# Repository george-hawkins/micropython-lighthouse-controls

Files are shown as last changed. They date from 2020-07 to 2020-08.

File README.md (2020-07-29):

MicroPython lighthouse controls
===============================

This project was created with [MicroPython](https://micropython.org/) running on an [ESP32](https://docs.espressif.com/projects/esp-idf/en/latest/esp32/hw-reference/esp32/get-started-devkitc.html) development board. The electronics drive the central mechanism for a toy lighthouse. The main point of this project, however, was to try and make something as close to a consumer product in terms of setup and ease of use.

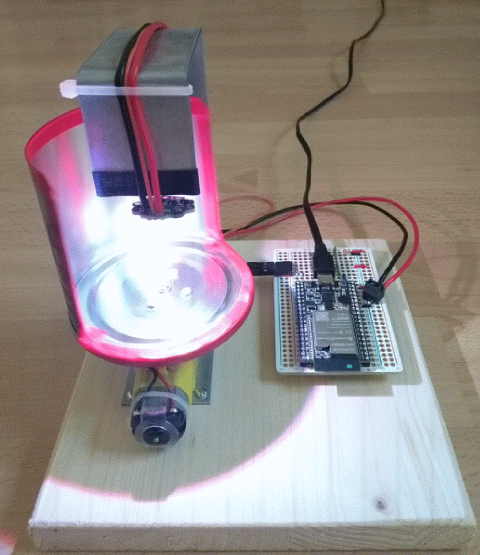
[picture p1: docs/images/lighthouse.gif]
lighthouse animated GIF


There are two main parts to making this device easy to use. The **first** part is connecting it to your network. The following is **not** a screenshot of the standard Android network selection interface. It's a web interface served out by the ESP32 to make it as easy to connect the device to a WiFi network as it is to do the same with your phone.

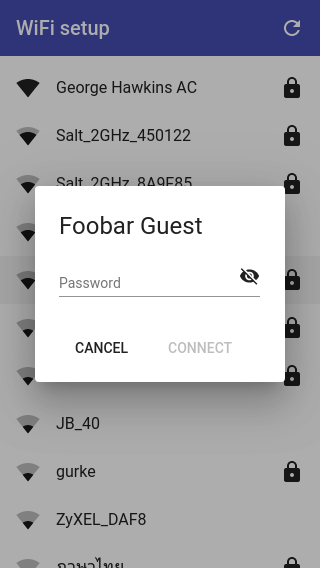
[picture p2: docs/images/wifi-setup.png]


As you may know, MicroPython on the ESP32 supports both an access point (AP) mode (where it behave as an AP that you can connect to) and a station (STA) mode (where it connects to an existing network). If this device cannot connect to an existing network, it creates an open AP that you can connect to and serves out the web interface shown above. Normally, when you create an access point like this, the client that connects to it still has to find the IP address of the device and then connect to that to access such an interface. The clever thing with this project is that it uses your system's captive-portal detection to connect you directly to the web interface when you connect to the network. Captive-portal detection is the same thing that pushes you to the login interface when you connect to public WiFi in places like coffee shops and airports. In this case, instead of a login page, you're presented with a web interface that shows you the networks that the device can see and lets you select the one to which you want to connect it.

The **second** part of making things easy to use is to provide a nice interface for controlling the device once it's connected to the desired network.

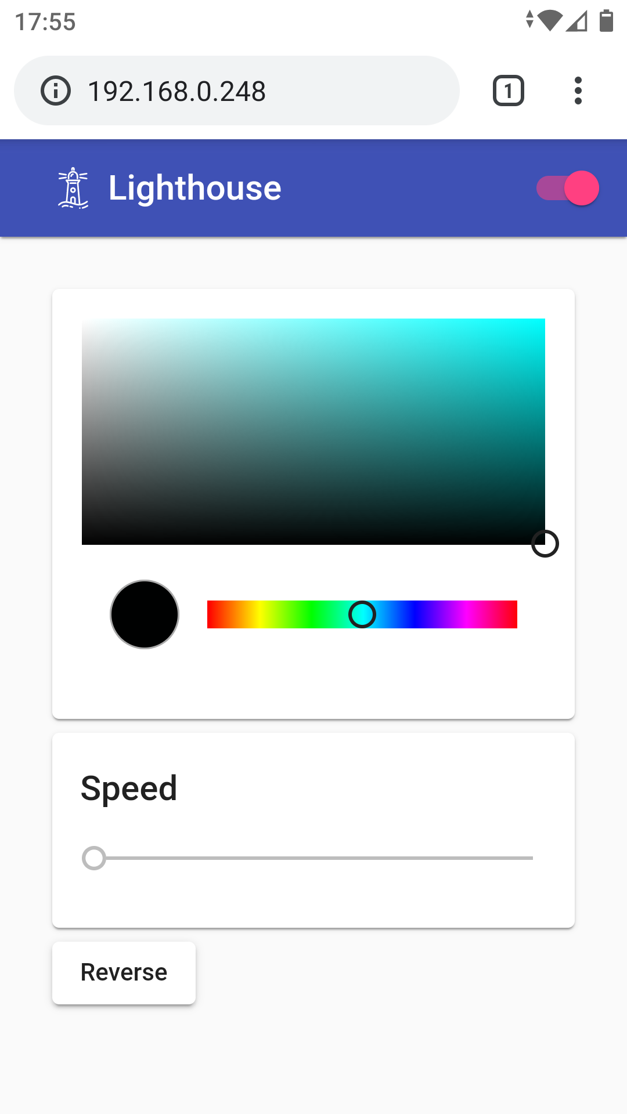
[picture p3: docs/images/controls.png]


Here, things are much easier than with the WiFi setup interface. The HTML etc. for the WiFi setup interface has to be stored locally on the device as, at this point, it has no access to the internet. However, once set up, the web interface for working with the device can be stored remotely (e.g. on GitHub). This saves storage and is also much quicker to load (GitHub being much quicker at serving web pages than an ESP32). A tiny main page for the interface above is retrieved by the device from GitHub and then served out to any requesting client. Then all other requests, related to loading the page, go directly to GitHub. The device serves out the main page (rather than simply doing a redirect) so that all subsequent Javascript etc. sees the device, rather than GitHub, as the origin. This is also important for all the rules related to insecure content loading secure content and vice-versa. It's fine for the device to serve out the main page via HTTP and then include content from GitHub via HTTPS. The opposite is not true, i.e. secure content cannot go on to include insecure content. This is important as the web interface, once served out and running in the client web browser, communicates with the device via a websocket. The websocket connection is insecure, i.e. uses `ws://` rather than `wss://`, and for this to be allowed by the client browser the containing page also has to have been served insecurely.

In the interface above, you can control:

* The brightness and color of the lighthouse light (it uses an RGB LED).
* The speed at which the motor turns.
* The direction the motor turns.

You can also turn off the device (the red slide-toggle), this puts the device into deep sleep.

Code
----

Interestingly, the bulk of the code involved is the WiFi setup code. This code has its own repo - [micropython-wifi-setup](https://github.com/george-hawkins/micropython-wifi-setup/) - where it's described in excessive detail.

The [Angular](https://angular.io/) and [Angular Material](https://material.angular.io/guide/getting-started) resources for the device's user interface (the controls seen above) also have their own repo - [material-lighthouse-controls](https://github.com/george-hawkins/material-lighthouse-controls).

This repo contains the MicroPython code that pulls everything together, it invokes the WiFi setup code and, once set up, it serves out the device's user interface and communicates with it via a websocket. It takes the commands received via the websocket and translates them into hardware actions.

Note: if you look at the code, you'll see that multiple people can open the device's web interface at the same time, each with their own websocket connection to the device. One person can reverse the motor direction while another changes the LED color.

The code here consists of:

* [`main.py`](main.py) - sets up the WiFi connection, controls the RGB LED and motor and handles serving out the web interface and accepting websocket connections.
* [`connect.py`](connect.py) - wraps up calling the WiFi setup logic provided by micropython-wifi-setup.
* [`message_extractor.py`](message_extractor.py) - provides a super-simple message layer on top of the raw websocket connection.

The messages, that I send via the websocket, consist of just a string delimited by the ASCII control characters STX and ETX (start and end of text, respectively). The sending logic in the Angular code contains throttling logic to ensure that it doesn't send messages faster than the device can process them (this would, otherwise, happen in particular when dragging your finger around in the color panel). However, the receiving logic also has logic to deal with this situation - it always tries to read as much data as is currently available and returns just the last message read for further processing, i.e. it will discard earlier messages if multiple messages come in at once. This is an acceptable strategy here as the discarded messages would e.g. be earlier speed values when dragging the speed slider - just processing the latest value is acceptable and is in fact desirable.

Breadboard and perma-proto layout
---------------------------------

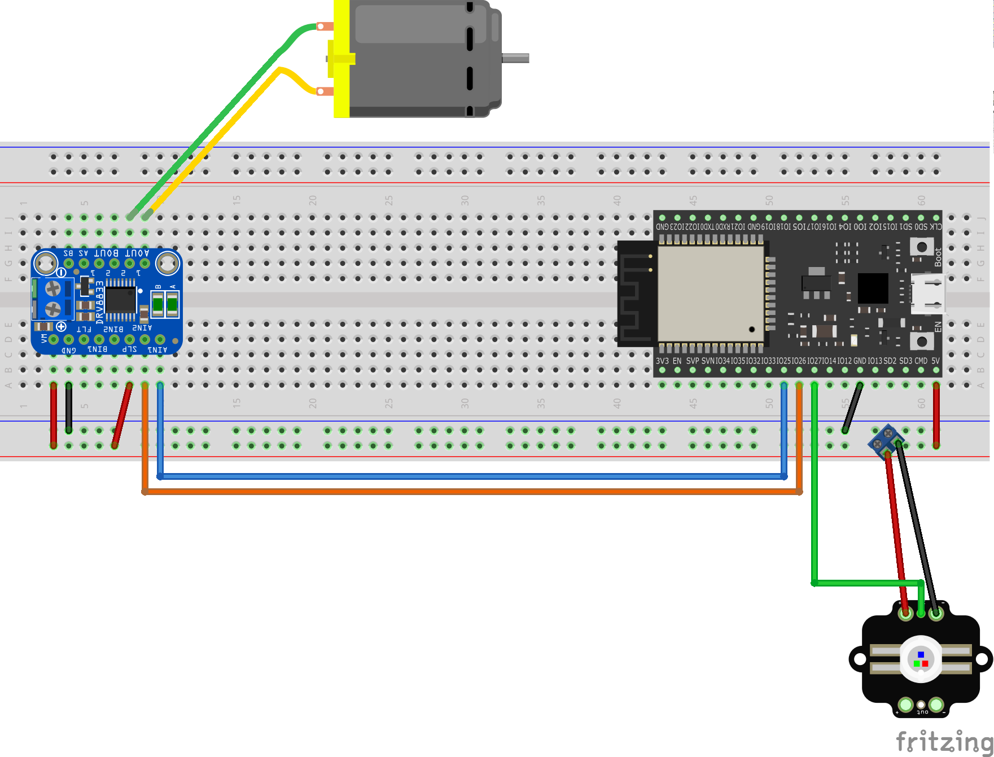
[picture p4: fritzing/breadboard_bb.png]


Fritzing file: [`fritzing/breadboard.fzz`](fritzing/breadboard.fzz)

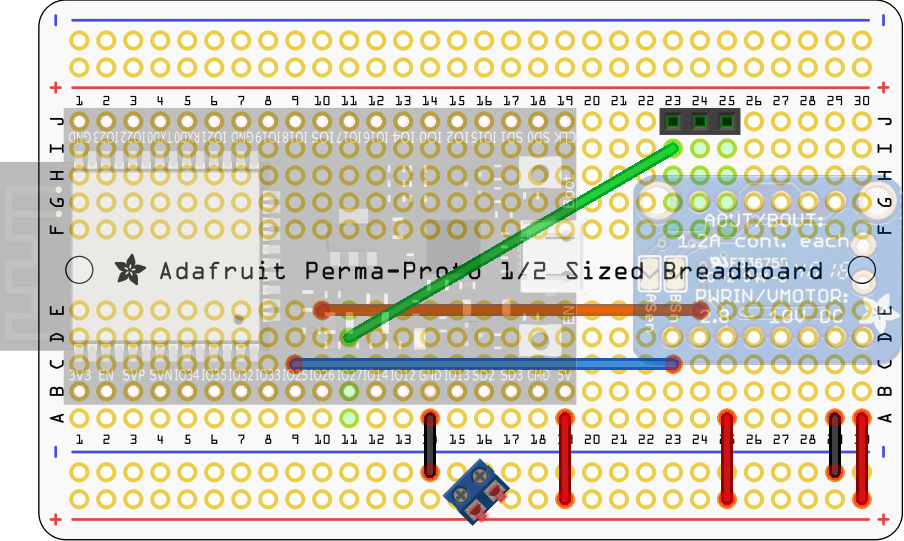
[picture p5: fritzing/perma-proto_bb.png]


Fritzing file: [`fritzing/perma-proto_bb.png`](fritzing/perma-proto_bb.png)

For the perma-proto layout, the DevKitC board was mounted on the top-side of the perma-proto board and the DRV8833 breakout on the underside. They're both shown in very transparent form here, so you can see where they go without obscuring the wiring.

I went for this layout as I wanted the PCB antenna of the DevKitC board to face outward over the edge of the perm-proto board and didn't want the DRV8833 breakout blocking access to the micro-USB connector of the DevKitC board.

All the wiring was done on the top of the perma-proto board except the green wire. Right-angle header was used for the header seen top-right and is where the wires to the motor and the control wire for the RGB LED are connected. The terminal block, seen bottom-center, is for the power wires for the RGB LED.

Note: I included a [0.1uF ceramic capacitor](https://www.adafruit.com/product/753) across the GND and VM pins of the DRV8833 breakout board. This isn't shown in the Fritzing diagrams above, but you can see it clearly in the picture of the top of the perma-proto layout found [here](docs/steps.md). This capacitor was included as a lucky talisman against any noise from the motor - but if the noise was a real problem then the proper way to deal with this would be capacitors soldered across the motor terminals and to its case as shown [here](https://learn.adafruit.com/adafruit-motor-shield-v2-for-arduino/faq) (for more details expand the answer to the question "When the motors start running nothing else works?"). Pololu also have a [page on this](https://www.pololu.com/docs/0J15/9).

I wanted to mount the perma-proto board on the wooden base using spacers with snap-in connectors (rather than the usual screws) but noticed too late that I'd blocked the perma-protos second mounting hole with the DRV8833 breakout board. Snap-in connectors would have allowed the mounting hole under the DevKitC to be used without needing to be able to get at the top-side of the mounting hole (as you would if using screws). It would have been just about possible to position the DRV8833 breakout board such that it didn't block the mounting hole but it would have made everything a very tight fit.

Parts
-----

More parts than you might expect were used in building this setup. The parts and prices are covered in [`docs/parts.md`](docs/parts.md).

Assembly
--------

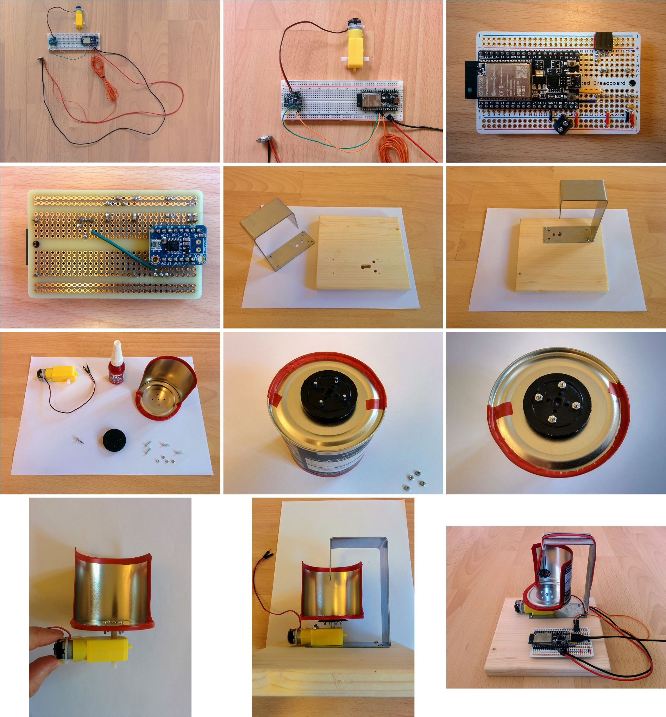
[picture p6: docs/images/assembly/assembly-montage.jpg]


For a step-by-step walkthru of the assembly see [`docs/steps.md`](docs/steps.md).

Installing the code
-------------------

Clone this repo and the micropython-wifi-setup repo and link to its `lib` directory:

    $ git clone git@github.com:george-hawkins/micropython-wifi-setup.git
    $ git clone git@github.com:george-hawkins/micropython-lighthouse-controls.git
    $ cd micropython-lighthouse-controls
    $ ln -s ../micropython-wifi-setup/lib .

Then create a Python venv and install [`rshell`](https://github.com/dhylands/rshell):

    $ python3 -m venv env
    $ source env/bin/activate
    $ pip install --upgrade pip
    $ pip install rshell

Then install everything on your board, start the REPL and then press the _EN_ or _reset_ button on your board:

    $ rshell --buffer-size 512 --quiet -p $PORT
    > mkdir /pyboard/lib
    > cp -r lib/* /pyboard/lib
    > cp main.py connect.py message_extractor.py /pyboard
    > repl
    ...
    I (1567) cpu_start: Pro cpu start user code
    ...
    INFO:captive_portal:captive portal web server and DNS started on 192.168.4.1

Replace `$PORT` with the serial device of your board (typically `/dev/ttyUSB0` on Linux and `/dev/cu.SLAB_USBtoUART` on Mac).

Then connect your device to your network as described in step 2 and onward [here](https://github.com/george-hawkins/micropython-wifi-setup/blob/master/docs/steps.md). At the end, instead of the cute little ghost placeholder shown there, you should see the lighthouse web interface.

Room for improvement
--------------------

At the moment the web interface does not detect if the device has been turned off (interestingly, it fairly quickly notices the issue when the device is started again, at which point it closes and reestablishes the connection). This is covered in more detail in the notes (see below) and could be addressed by sending heartbeats in both directions (from browser to device and vice-versa).

It would be nice to use mDNS, rather than raw IP addresses, where supported (i.e. most modern operating systems). However, there's currently a bug in the ESP-IDF mDNS implementation (again see the notes for more details). It's also the case that mDNS sometimes doesn't work for odd local network reasons or due to how name resolution is configured on the system making the requests - so while a raw IP address is guaranteed to almost always work the same is not true of an mDNS name. So ideally one would connect initially using a raw IP address and then using some AJAX logic behind the scenes e.g. ask the device for its mDNS name, see if it can be accessed by this name and if so use it rather than the IP address from then on.

Notes
-----

For further notes see [docs/NOTES.md](docs/NOTES.md).

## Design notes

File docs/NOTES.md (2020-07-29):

NOTES
=====

This page contains miscellaneous notes that were accumulated in the process of creating this project.

Thermal cut-off
---------------

At full brightness, the Pixie heats up very quickly and the temperature cut-off kicks in (as it should). However, such a limited running time at maximum brightness makes the Pixie a little pointless, i.e. why have a 3W LED if you have to run it at lower power? Maybe, using a thermally conductive pad to connect it to the metal frame would solve this issue:

* Banggood 5mm thick [thermal pad](https://www.banggood.com/100mmx100mmx5mm-GPU-CPU-Heatsink-Cooler-Blue-Thermal-Conductive-Silicone-Pad-p-989163.html).
* Arctic 1mm thick [thermal pad](https://www.arctic.ac/ch_en/thermal-pad.html).

Note that 1mm thickness seems to be the norm, the 5mm thickness from Banggod is unusual. No one actually seems to have this kind of thing in stock at the moment (possibly due to COVID-19 related shipping issues).

Given the Pixies exposed components, you obviously want a terminally conductive material that is _not_ electrically conductive.

Tining wires
------------

The power wires are tinned on the ends that are soldered into the Pixie. They are **not** tinned on the ends that are inserted into the screw terminal block. It may seem convenient to tin the ends to stop the wire strands splaying out but for a clear explanation of why this is a bad idea, see [this](https://electronics.stackexchange.com/a/29862/27099) Electronics StackExchange answer and [this](https://reprap.org/wiki/Wire_termination_for_screw_terminals) RepRap wiki entry on the topic.

mDNS
----

It would be nice if we could use [mDNS](https://en.wikipedia.org/wiki/Multicast_DNS) and indeed MicroPython supports advertising the device name via mDNS (and I take advantage of that support). However, at the moment there is a bug in the ESP-IDF mDNS functionality that means that some systems will reject the ESP-IDF generated mDNS responses. For more details see ESP-IDF bug [#5574](https://github.com/espressif/esp-idf/issues/5574) (I've also commented about this on MicroPython issue [#4912](https://github.com/micropython/micropython/issues/4912) that covered adding the necessary mDNS support to MicroPython).

LightDims
---------

The blindingly bright red LED of the DevKitC board can be blocked with a small black-out edition LightDim shape (see [here](https://www.lightdims.com/store.htm)), I find them far more effective than e.g. black duct tape.

Websocket closure
-----------------

The Angular web UI doesn't typically become aware of the remote end, of the websocket connection, disappearing (or at least it takes it a long time to notice). I added a heartbeat in the hope that actively trying to push data would trigger the lower level logic to notice any disconnect quicker but this didn't improve things. If I look at the sockets involved, I see that they remain in `ESTABLISHED` state even if the remote device has been completely switched off:

    $ sudo netstat -nap | fgrep 192.168.0.248
    tcp        0   2048 192.168.0.241:45774     192.168.0.248:80        ESTABLISHED 3884/chrome --type=

Here, 192.168.0.248 is the address of the switched-off remote device. I'd expected to see the socket stuck in `FIN_WAIT1` state (a common issue when the remote end disappears without having had a chance to close its connections properly) but it doesn't seem to have even got that far - the system remains unaware that anything untoward has happened.

Instead of using `openObserver` and `closeObserver`, with the RxJS `webSocket` function, to track opening and closing, I should move to having both sides sending a heartbeat and treat the failure to receive such heartbeats as a disconnect.

Motor frequency and duty values
-------------------------------

The power supply is 5V and the motors can handle up to 6V so, when driving the motor, we don't need to cap the duty value below the maximum allowed value of 1023.

The minimum duty cycle and optimum frequency were found by experimentation. For the Adafruit 1:48 [DC gearbox motor](https://www.adafruit.com/product/3777), the results were:

* The duty value needs to be 240 or above for the motor to turn.
* At this value, the motor turns fastest with a frequency of about 100Hz.

You can't find the duty and frequency values independently, e.g. if you fix the frequency high and adjust the duty value, you'll end up with a much higher minimum duty value than if you fix the frequency low.

Ideally, you'd use a quadrature encoder to measure the turning speed. I just used slow-motion mode on my smartphone camera, captured about 5 seconds of video at various frequencies and counted the rotations.

If you set the frequency very low, e.g. 10, the motor clearly judders on and off. So for a smooth motion, it would seem obvious to set the frequency as high as possible. However, with the duty value at 300, the motor barely turns at a frequency above 2KHz. In fact, the turning speed starts dropping gradually as you go above 100Hz.

The "PWM Frequency" section of this [DesignSpark article](https://www.rs-online.com/designspark/spinning-the-wheels-interfacing-pmdc-motors-to-a-microcontroller) includes a _possible_ explanation:

> One explanation may be that the very narrow pulses of a high-frequency signal are just not long enough to 'kick' the rotor into action.

I've asked about this [here](https://electronics.stackexchange.com/q/509426/27099) on the Electronics StackExchange.

Changing motor direction
------------------------

When you press _Reverse_ in the web interface, the code in [`main.py`](../main.py) slows the motor to a stop and then speeds it back up in the opposite direction. This not only prevents a sudden jolt, in going immediately from a given speed in one direction to going the same speed in the opposite direction, it also prevents a sudden jump in the current drawn by the motor which _could_ otherwise be up to 20 times the normal free-running current consumption. For more details see the "Motor Considerations" section of this [Pololu page](https://www.pololu.com/docs/0J44/4.1) on motor controllers.

UART pins
---------

UART0 is used for the UART-to-USB bridge but UART1 and UART2 are available. However, I always got a [guru meditation error](https://docs.espressif.com/projects/esp-idf/en/latest/esp32/api-guides/fatal-errors.html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) after a small amount of interaction with either if I used their default pins (rx=9 and tx=10 for UART1 and rx=16 and tx=17 for UART2).

For whatever reason, everything works fine if I specify pretty much any other pins for tx and rx (it's a nice feature of the ESP32 that the UART pins are not fixed).

It seems to be a known issue that the default pins can be problematic, see MicroPython issue [#4997](https://github.com/micropython/micropython/issues/4997).

I chose pins 27 and 14 (which despite their numbers are beside each other on the board) for no particular reason. As I'm doing no receiving I've actually just left pin 14 floating but it might have been better to connect it to a pull-down resistor.

Note: when you initialize a UART, the ESP32 often (but not always) outputs a console message like this:

    I (7336) uart: ALREADY NULL

This sounds like an error but others have commented on it and it appears to be of no particular importance.

GitHub caching
--------------

The web interface is actually hosted on GitHub, the root page is retrieved in MicroPython and served out so that it appears to come from the device.

All modern browsers accept gzipped data but the request made by MicroPython does not signal that it will accept compressed data. This shows up something odd in how GitHub caches request responses.

If you accept gzipped data you quickly see any changes made to the hosted data on GitHub. However, if you do not, GitHub continues to serve out stale cached data long after the underlying data has changed.

If you use `-v` with `curl` and switch between using `--compressed` and omitting it, you can clearly see the different cache-related headers between the two situations.

I suspect this is some kind of bug on GitHub's part rather than a deliberate attempt to punish anyone requesting uncompressed data.

To get around this a query string with a UUID value is included in each request to bypass the caching.

Websocket command-line tool
---------------------------

For websocket experimentation, I used [`websocat`](https://github.com/vi/websocat) like so:

    $ websocat ws://192.168.0.248/socket

Or:

    $ websocat ws://ding-5cd80b3.local/socket

Undefined pin states
--------------------

As is usual with such devices, the ESP32 pin states are undefined during startup. I've seen the Pixie flicker during this period (but I've never seen the motor budge). For defined pin states, irrespective of the state of the ESP32, I'd:

* Add a pulldown resistor to the Pixie data wire.
* Control the SLP pin of the motor driver via the ESP32 (rather than wiring it directly to the perma-proto board's positive rail) and add a pulldown resistor to the relevant pin.

Then to enable the SLP pin in MicroPython, just do:

    slp = machine.Pin(27, machine.Pin.OUT)
    slp.on()

Lighthouse animation
--------------------

I produced the animated GIF using Google Lab's [Motion Stills app](https://play.google.com/store/apps/details?id=com.google.android.apps.motionstills).

Then after downloading it from Google Drive, I unpacked it into individual frames:

    $ mv ~/Downloads/lighthouse.gif .
    $ convert lighthouse.gif xx_%05d.gif

Then, by looking at the frames, I worked out that I only needed the first 16 for a full cycle. So I threw away the rest.

I then cropped the images to remove unwanted background:

    $ convert xx_* -crop 480x555+0+85 +repage yy_%05d.gif

And repacked the result:

    $ gifsicle --delay=5 --loop yy* > lighthouse-min.gif

Black and flake8
----------------

`black` and `flake8` are used as following with the Python files in this project:

    $ black *.py
    $ flake8 *.py | fgrep -v -e E501 -e E203

Note: `E501` and `E203` are simply rules that `black` and `flake8` disagree on.

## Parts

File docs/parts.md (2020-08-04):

Parts
=====

This page lists the various parts needed to build the lighthouse and its electronics.

Development board
-----------------

I used an Espressif ESP32 DevKitC **VB** board. Unlike most boards (which feature a basic WROOM module with just 520KiB of SRAM) this board has a WROVER module with an additional 4MiB of SRAM. This gives you a bit more space to work with when running more substantial MicroPython programs. It's available from many suppliers, including:

* [Mouser](https://www.mouser.com/ProductDetail/356-ESP32-DEVKITC-VB) - US$10 (postage not included).
* [Banggood](https://www.banggood.com/ESP32-DevkitC-Core-Board-ESP32-Development-Board-ESP32-WROOM-32U32D-F-VB-VIB-S1-p-1426780.html?ID=566841) - US$18 (postage included).

Adafruit parts
--------------

* [Adafruit Pixie](https://www.adafruit.com/product/2741) -  $15
* [1:48 plastic gearbox motor](https://www.adafruit.com/product/3777) - $3
* [Motor pulley](https://www.adafruit.com/product/3789) - $0.75
* [DRV8833 motor driver breakout](https://www.adafruit.com/product/3297) - $5
* [Half-sized perma-proto board](https://www.adafruit.com/product/1609) - $4.50
* [2-pin 3.5mm terminal block](https://www.adafruit.com/product/724) - $3

All these items are available directly from [Adafruit](https://www.adafruit.com/) but they're also available through lots of [distributors](https://www.adafruit.com/distributors), in particular, all these items are available via [Mouser](https://www.mouser.com/) and [Digikey](https://www.digikey.com/).

I used Mouser for my order as it meant I could get the Adafruit items and additional parts like the ESP32 DevKitC VB all together.

If I was doing this again, I'd use a motor and motor driver from Pololu instead, see below for more details.

Light cover
-----------

The half-open/half-closed cover for the lighthouse light was cut from a standard tin can (I chose one with a nice shiny metal interior).  I used a tin-snips (like [this one](https://www.stanleytools.com/products/hand-tools/cutting-tools/snips/fatmax-straight-cut-compound-action-aviation-snips/14-563)) to cut it down to size and then covered the exposed edges with duct tape to make them less of an accident risk.

I initially bought a tin-snips for cutting circuit boards (where it does a so-so job) but have since found them great for cutting all kinds of material - you can cut surprisingly straight lines with them through material like a tin can.

Bolts and threadlocker
----------------------

* M2 10mm bolts with corresponding nuts (something like [these](https://www.conrad.com/p/toolcraft-827129-fillister-head-screws-m2-10-mm-phillips-din-7985-steel-zinc-galvanized-100-pcs-827129) with these [nuts](https://www.conrad.com/p/toolcraft-815608-hexagonal-nuts-m2-din-934-steel-zinc-plated-100-pcs-815608)) - for attaching the tin can to the motor pulley.
* 2.5x16mm round-headed wood screws (something like [these](https://www.homebase.co.uk/wood-screw-round-head-brass-3-x-12mm-10-pack_p168370) but different dimensions) - for attaching the metal frame to the base.
* M2.5 25mm bolts with corresponding nuts (something like [these](https://www.conrad.com/p/toolcraft-145896-fillister-head-screws-m25-25-mm-phillips-din-7985-steel-zinc-galvanized-200-pcs-145896) with these [nuts](https://www.conrad.com/p/toolcraft-815616-hexagonal-nuts-m25-din-934-steel-zinc-plated-100-pcs-815616)) - for bolting the motor to the frame.
* Loctite 243 threadlocker - to prevent bolts from rattling loose due to motor vibration.

Note that Loctite 243 isn't so strong that you can't subsequently undo the bolts (there are stronger threadlocker formulations which are essentially permanent).

Base and frame
--------------

* 1m x 35.5mm x 1.5mm galvanized flat steel bar for the frame (something like [this](https://www.homebase.co.uk/galvanised-steel-flat-bar-profile-1m-x-35-5mm_p414991)).
* 160cm x 150cm x 24mm spruce plywood for the base.

Wire
----

* 20AWG silicone-coated stranded wire - 1m black and 1m red for the Pixie power wires.
* 26AWG silicone-coated stranded wire - 1m for the Pixie data wire (26AWG is the standard thickness for jumper wires).
* Solid core hookup wire (like [this](https://www.adafruit.com/product/1311)) - for wiring up the perma-proto board.

The Pixie [hookup guide](https://learn.adafruit.com/pixie-3-watt-smart-chainable-led-pixels?view=all) recommends 16AWG wire for the Pixie power wires. This is complete overkill if you're only planning on using a single Pixie (which will draw, at most, 1A). I accidentally used 18AWG wire when I intended to use 20AWG wire. The terminal block (up above) is rated for 30-16AWG wire according to the Adafruit product page. However, it's very inconvenient to use stranded 18AWG wire with them and 16AWG wire definitely would be too fat for the holes.

Note: I crimped the non-soldered end of the Pixie data wire with a crimping tool like [this](https://www.pololu.com/product/1929) and used a crimp pin like [this](https://www.pololu.com/product/1931) with a connector housing like [this](https://www.pololu.com/product/1900).

Bits and pieces
---------------

* right-angle female header (i.e. something like [this](https://www.adafruit.com/product/1542) cut down to just three sockets) - for connecting the Pixie data and motor wires to the perm-proto board.
* 0.1uF ceramic capacitor (like [these](https://www.adafruit.com/product/753)) - lucky charm talisman for reducing motor noise.
* 200mm x 2.5mm cable-ties - to hold the Pixie wiring in-place on the frame.

Power supply
------------

The motor and in particular the 3W RGB LED draw a lot more current than most small electronics projects and certainly a lot more than the 500mA typically provided by your computer's USB ports (though, during development, you can run both the motor and RGB LED from such a port if you keep the speed and brightness low).

So make sure that the micro-USB power adapter, that you use, can supply at least 2A at 5V. The older style 2.5A Raspberry Pi power adapters are perfect (the newer style ones come with a USB-C connector). RS supply the classic style Raspberry Pi power adapters with region-specific plugs, just go to [RS Components](https://www.rs-online.com/), choose your region (for North American, choose the Allied link rather than the RS link) and search for:

* T6717DV for a US-style plug.
* T6716DV for an EU-style plug.
* T6715DV for a UK-style plug.

These are the standard Raspberry Pi power supplies and are available from many other online retailers - just search for the part numbers in Google Shopping.

Continually connecting and disconnecting the micro-USB is likely to end in damage to the board. A better solution is something like this:

* [micro-USB to micro-USB on-off switch](https://www.reichelt.com/ch/en/raspberry-pi-cable-with-switch-30-cm-black-rpi-cable-sw-30-p223610.html) - $3.

Note that this particular cable does not support data transfer.

Pololu
------

[Adafruit](https://www.adafruit.com/) and [Sparkfun](https://www.sparkfun.com/) are great for hobbyist electronics parts. However, for electro-mechanical parts, Pololu is a much better source. Adafruit and Sparkfun just carry a few stepper motors and gearbox motors, whereas Pololu specialize in these kinds of parts and carry full ranges of different kinds of motors - so you can choose exactly what you want for a particular project. And all their other parts play well in electro-mechanical projects, e.g. I had some jumper wires from Adafruit that would be perfect for nearly any electronics project but couldn't carry enough current for a [rover](https://www.pololu.com/category/202/romi-chassis-and-accessories) project, that I was doing, but the corresponding Pololu wires worked perfectly (and were much nicer to use as they were silicone-coated rather than plastic-coated).

The Adafruit motor listed above has a gear ratio of 1:48. Even at minimum speed it still turns quite quickly (the motor has a minimum speed below which it simply comes to a stop).

Pololu offer similar motors with more appropriate gear ratios:

* [120:1](https://www.pololu.com/product/1121)
* [200:1](https://www.pololu.com/product/1120)

Pololu also provide a [DRV8833 motor driver breakout](https://www.pololu.com/product/2130) that's essentially identical to the Adafruit breakout.

Note: Adafruit also offer an [1:90 gearbox motor](https://www.adafruit.com/product/3801) that would also have been a better initial choice.

3W RGB LED
----------

I used a $15 Adafruit Pixie for the RGB LED component of this project. Initially, I looked at using Adafruit's basic [3W RGB common anode LED](https://www.adafruit.com/product/2530) which is a lot cheaper at just $3. However, after some experimentation, it's clear that these things get _extremely_ hot if run at full brightness. So the additional thermal-cutoff circuitry of the Pixie seemed worth the additional cost to avoid the risk of setting my apartment on fire.

Note that the basic 3W RGB LED isn't as cheap as it seems, as the Pixie includes the necessary additional FETs and limiting resistors. With the basic 3W RGB LED, you'd also need three [IRLB8721 N-channel power MOSFETs](https://www.adafruit.com/product/355) (these are available for about half the Adafruit price from suppliers like Mouser or Digikey) and a 1W or 0.5W limiting resistor for the red element of the LED (the resistors that you use for most simple electronics projects are usually 0.25W resistors). You also have to factor in the additional time cost of soldering in these components and the fairly considerable extra space that these non-SMT components take up.

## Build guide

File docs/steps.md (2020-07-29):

Assembling the lighthouse
=========================

Breadboard layout.  
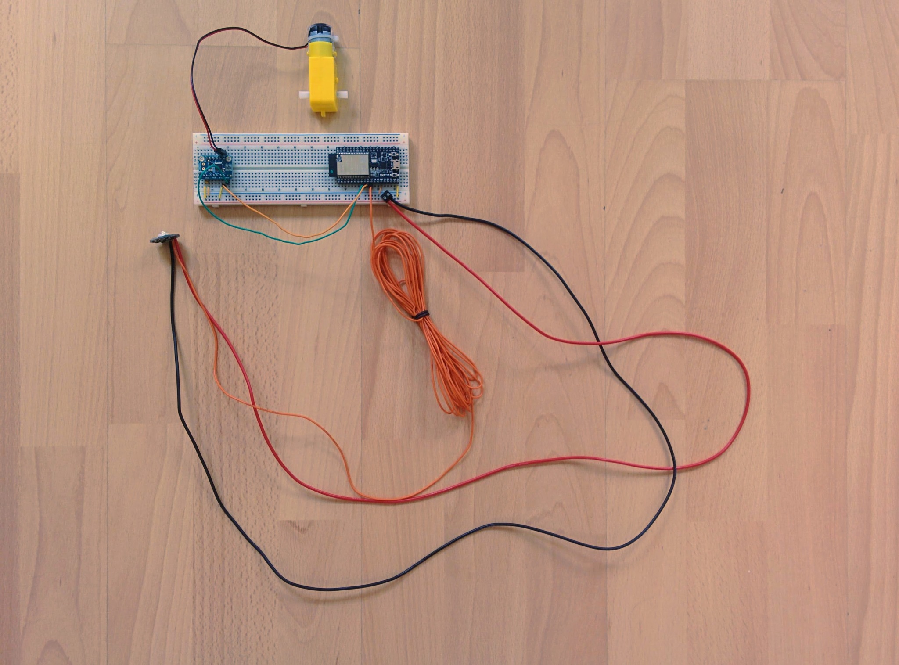
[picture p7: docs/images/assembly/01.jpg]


Breadboard layout closeup.  
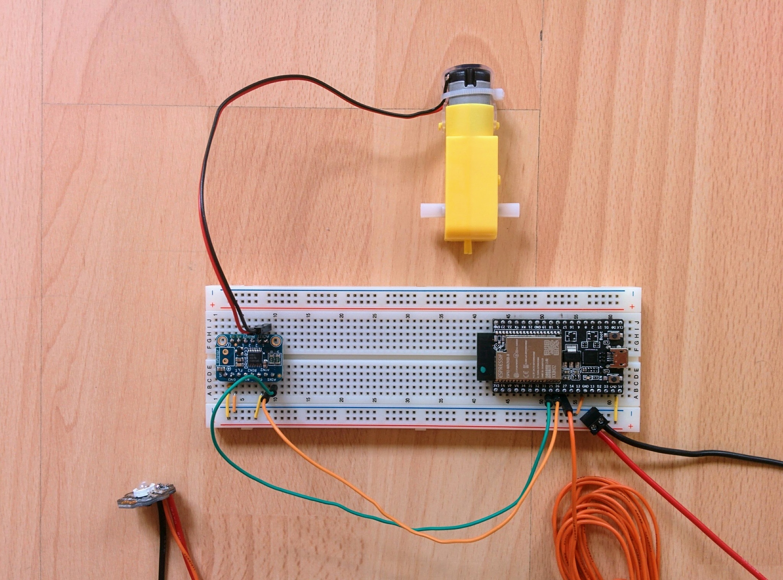
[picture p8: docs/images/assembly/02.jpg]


Perma-proto layout - top.  
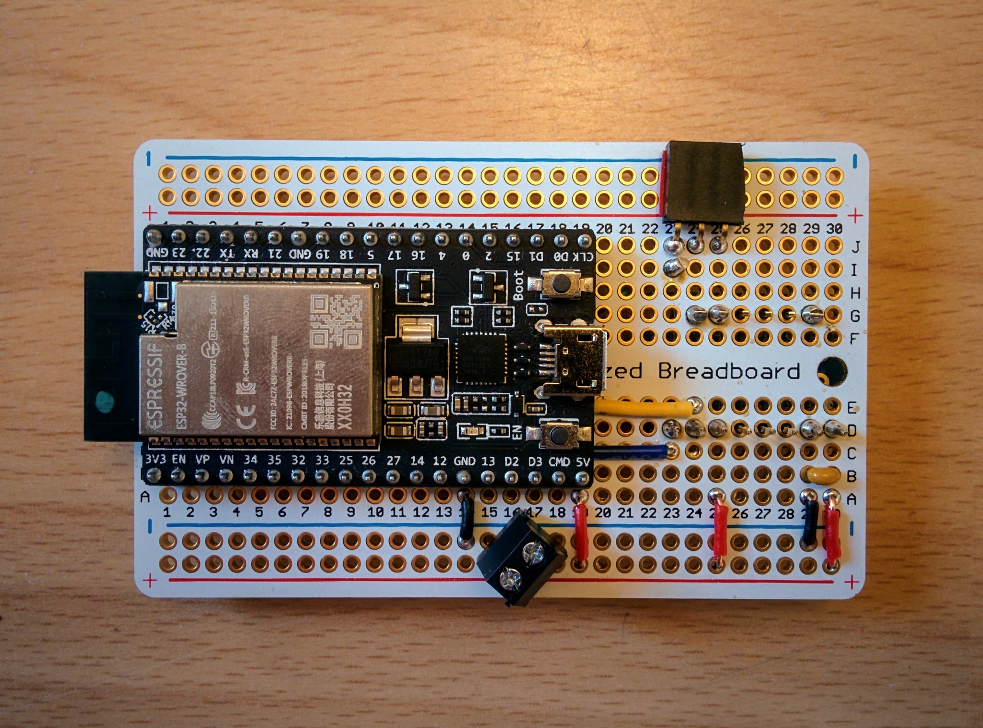
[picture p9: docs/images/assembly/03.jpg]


Perma-proto layout - bottom.  
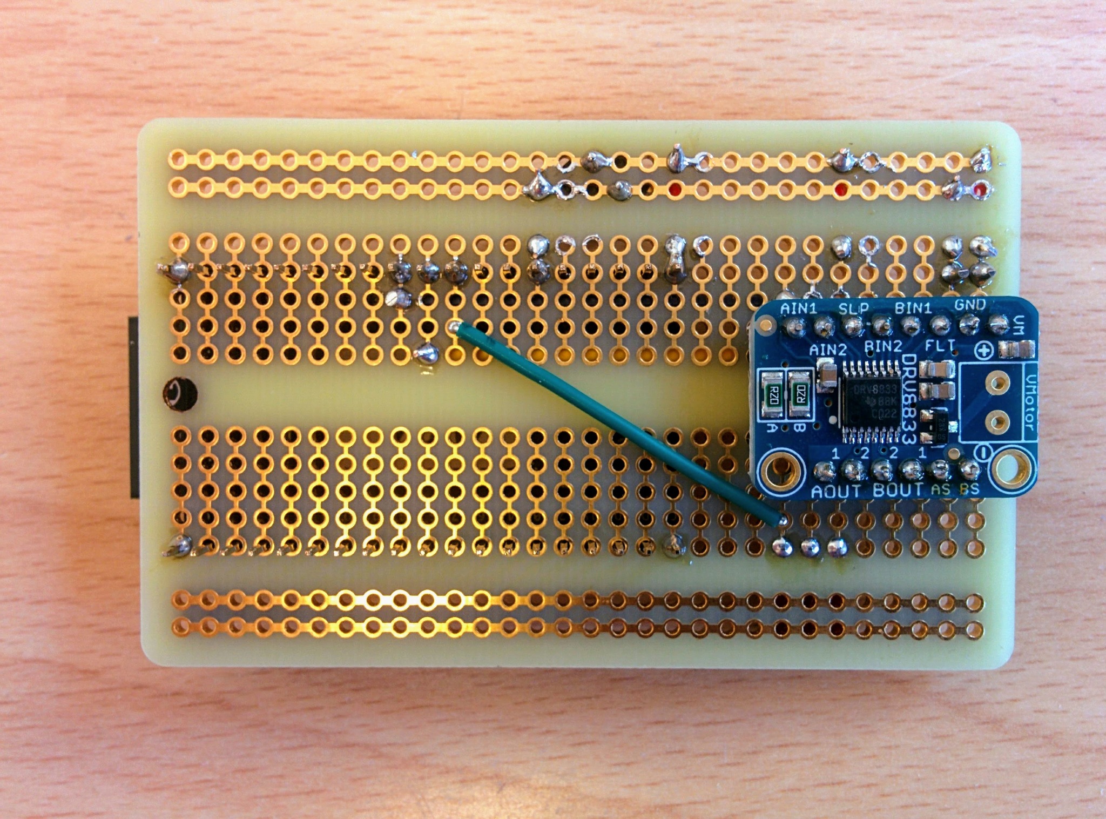
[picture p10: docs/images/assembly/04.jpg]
  
<sub>It's not the neatest soldering job ever - the solder spread out surprisingly easily to adjacent holes and had to be tidied up.</sub>

Flat steel bar cut down to size and drilled.  
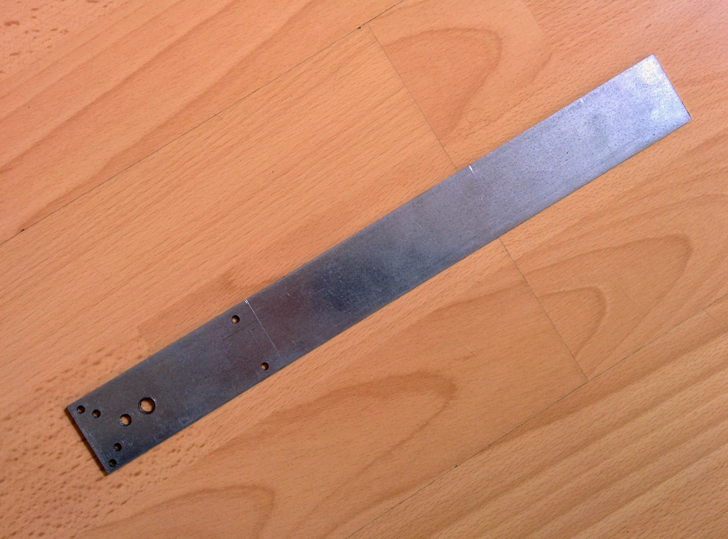
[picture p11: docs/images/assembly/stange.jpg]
  
<sub>And then bent into shape with a bending machine. This was all done at my local machine-tools center (the [Dynamo Machinenpark](https://www.dynamo.ch/maschinenpark)).</sub>

Wooden base and metal frame.  
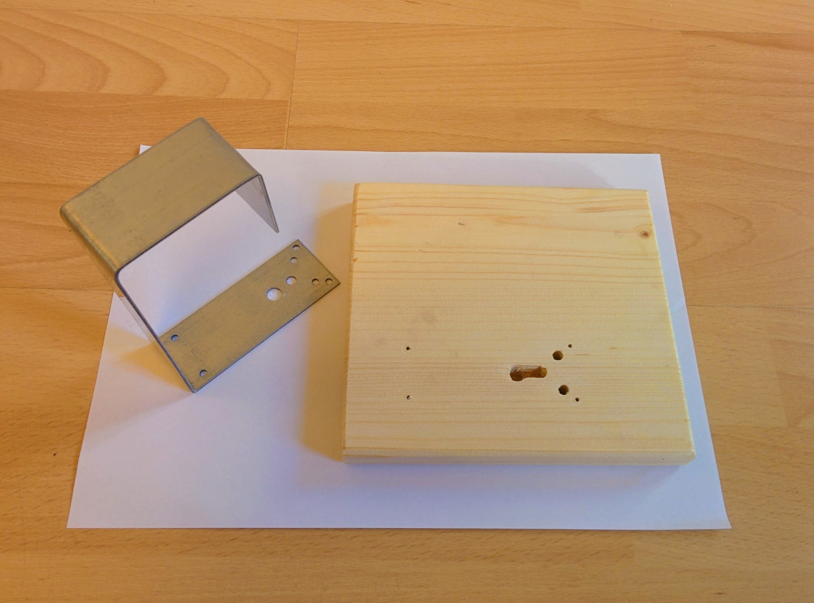
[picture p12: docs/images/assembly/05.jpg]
  
<sub>I drilled two separate holes for the downward-facing drive shaft and the lug on the underside of the motor casing. However, the wood between the two splintered so I ended up with the elongated looking hole that you see here.</sub>

Frame attached to base.  
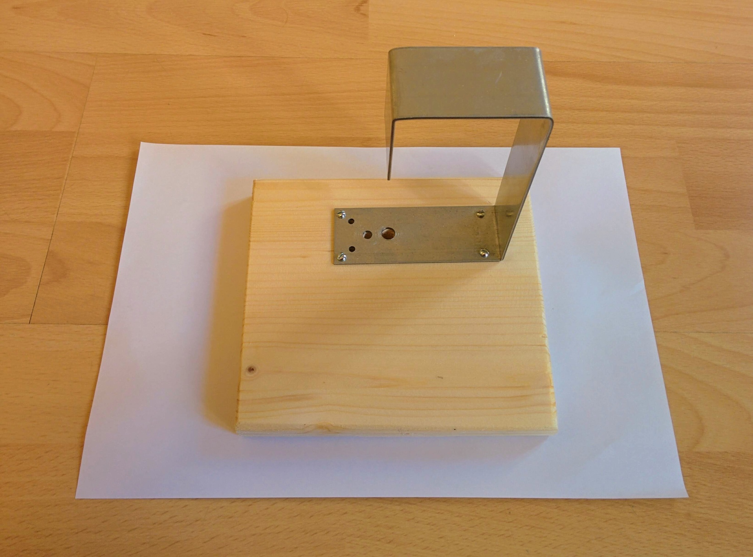
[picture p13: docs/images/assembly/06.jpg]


Motor and parts for the main assembly to be attached to the drive shaft.  
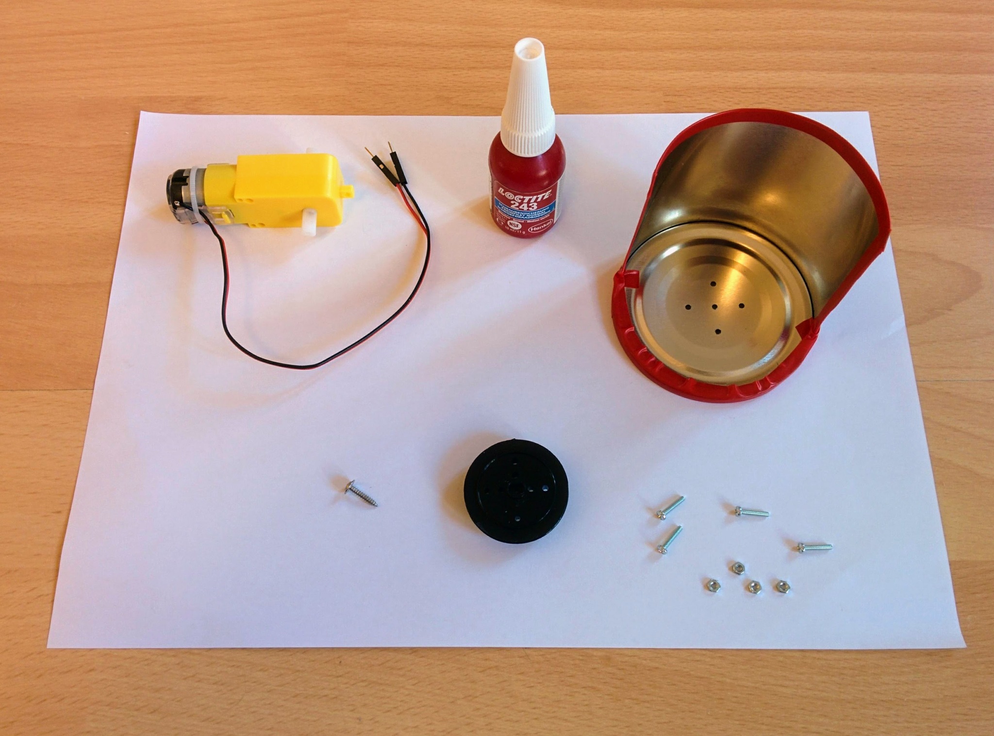
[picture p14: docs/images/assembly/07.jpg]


Threadlocker (blue) applied to the bolts.  
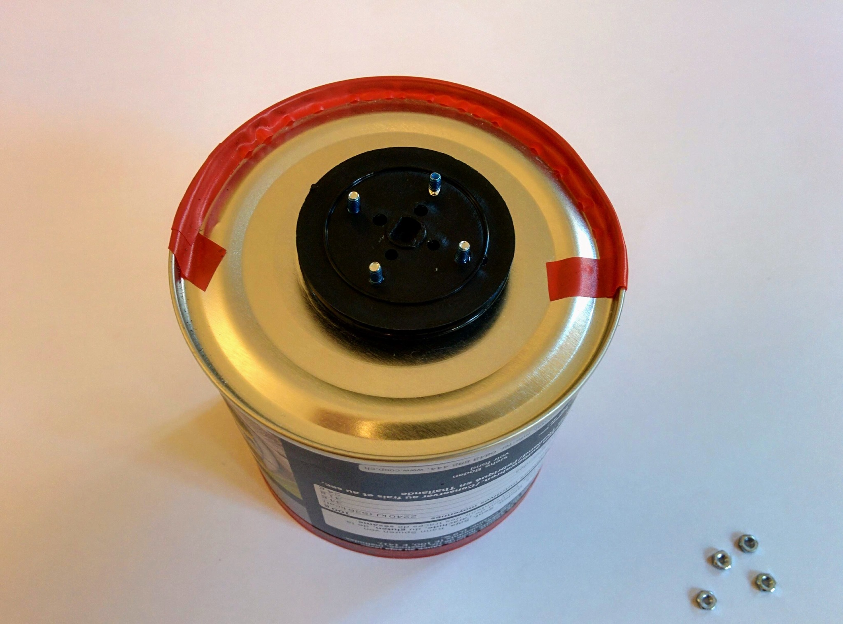
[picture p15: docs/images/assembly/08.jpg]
  
<sub>I also used Blu Tack as filler between the plastic disk and the base of the tin.</sub>

Nuts in place.  
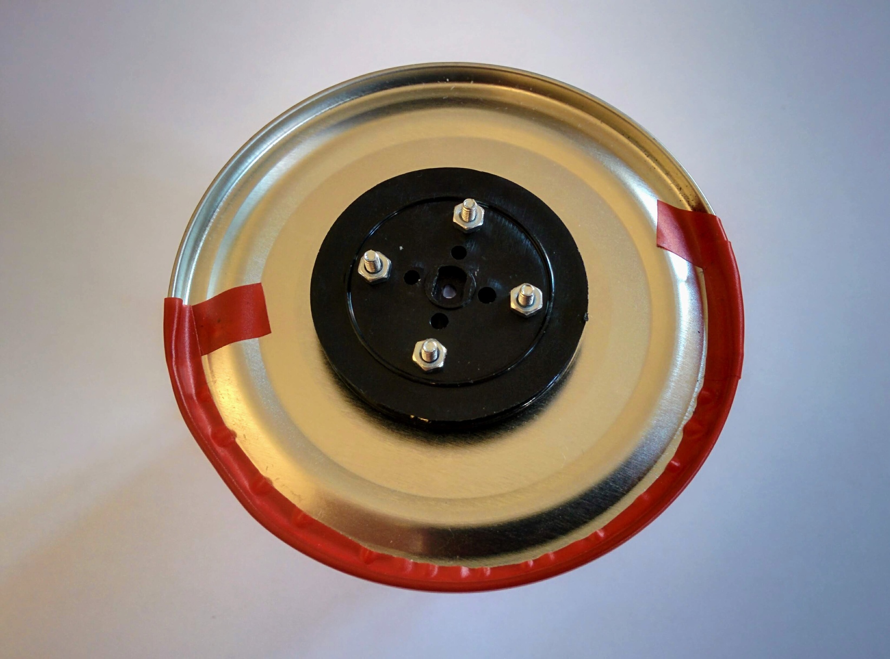
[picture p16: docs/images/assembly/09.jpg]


Main assembly screwed onto drive shaft.  
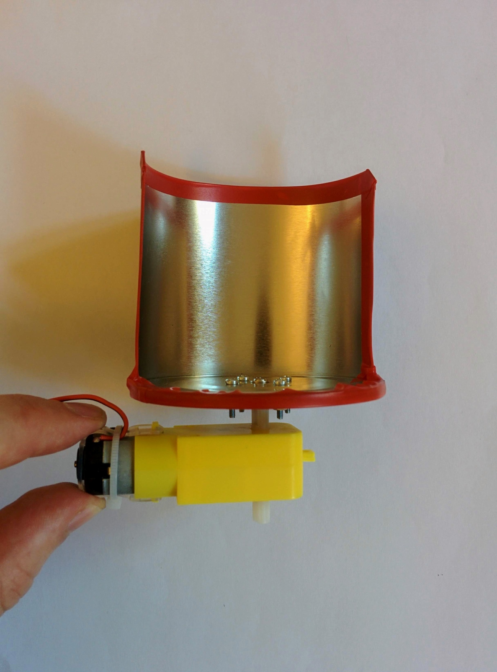
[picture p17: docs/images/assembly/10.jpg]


Motor bolted into place on base.  
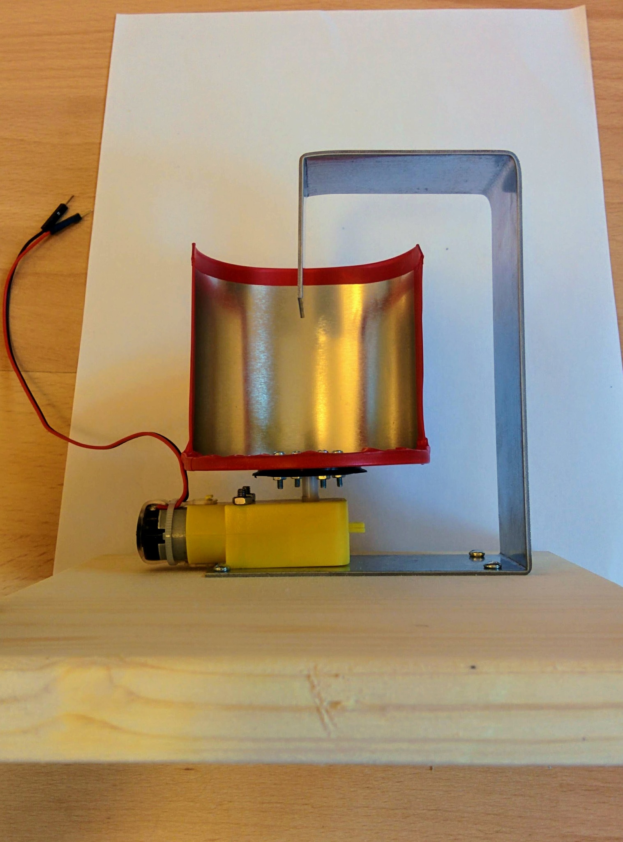
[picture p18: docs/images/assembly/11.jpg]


Electronics attached and ready to go.  
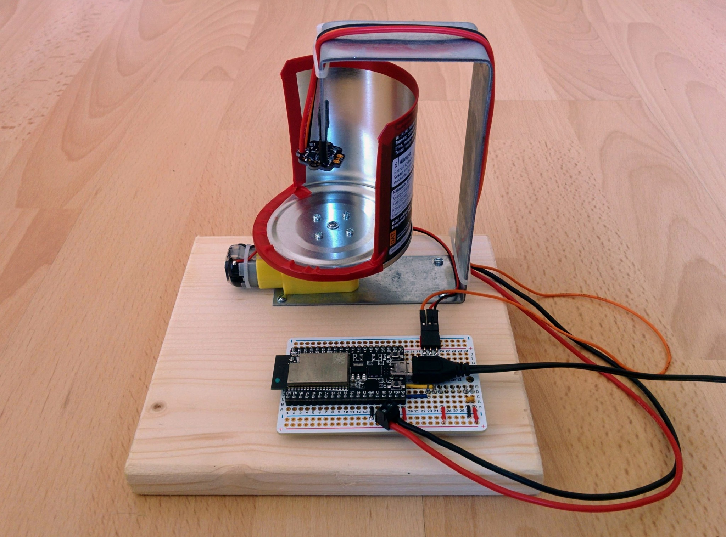
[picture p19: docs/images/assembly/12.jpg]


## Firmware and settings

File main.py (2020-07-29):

import machine
import time
import select
import sys
import urequests as requests  # For some reason urequests isn't available directly as requests (MP 1.12).

from os import urandom
from binascii import hexlify

from slim.slim_server import SlimServer
from slim.web_route_module import WebRouteModule, RegisteredRoute, HttpMethod
from slim.ws_manager import WsManager
from message_extractor import Extractor
from schedule import Scheduler
from logging import getLogger
from connect import connect

# --------------------------------------------------------------------------------------

logger = getLogger("main")

# Establish a WiFi connection using all the cleverness of https://github.com/george-hawkins/micropython-wifi-setup
connect()

# --------------------------------------------------------------------------------------

# Setup the Adafruit Pixie.

# See docs/NOTES.md for why the default tx and rx values for UART1 are overridden.
pixie = machine.UART(1, tx=27, rx=14)

color = memoryview(bytearray(3))


def refresh_color():
    pixie.write(bytes(color))


def set_color(new_color):
    assert len(new_color) == 3
    color[:] = new_color
    refresh_color()


# The Pixie color values must be rewritten at least every 2 seconds otherwise it turns off.
# This is to prevent it getting stuck bright (and hot) if the controlling board hangs.
REFRESH_DELAY = 1  # 1s

schedule = Scheduler()

schedule.every(REFRESH_DELAY).seconds.do(refresh_color)

# --------------------------------------------------------------------------------------

# Setup the A1N1 and A1N2 pins on the Adafruit DRV8833 motor driver breakout.

a1n1 = machine.PWM(machine.Pin(25))
a1n2 = machine.PWM(machine.Pin(26))

# See README for how `FREQUENCY` and duty values were arrived at.
# The motor will usually start at around 240 but this seems to depend on whether it's warmed up and other factors.
# 270 is high enough that it almost always starts even at 1% speed.
FREQUENCY = 100
MIN_DUTY = 270

# The maximum value of 1023 is fine in terms of not exceeding the motor's maximum voltage.
# However, it's far too high a maximum speed for what's supposed to be a lighthouse.
DUTY_RANGE = 200
assert MIN_DUTY + DUTY_RANGE < 1023

# Note that soft-reboots don't reset PWM values.
a1n1.freq(FREQUENCY)
a1n2.freq(FREQUENCY)
a1n1.duty(0)
a1n2.duty(0)

# --------------------------------------------------------------------------------------

DELAY = 2  # 2ms

speed = 0
_dir = 1  # Underscore used to avoid clash with existing global with same name.
pin = a1n1

# Functions for controlling the speed and direction of the motor.


def speed_to_duty(_speed):
    return int(DUTY_RANGE * _speed / 100 + MIN_DUTY)


def reverse():
    global _dir, pin
    current = speed
    set_speed(0)
    _dir *= -1
    pin = a1n1 if pin == a1n2 else a1n2
    set_speed(current)


# Smoothly increase or decrease from current speed to new speed rather than juddering straight one to the other.
# Changing from 0 to 100% takes about 1.5s, change `DELAY` to increase or decrease this.
def set_speed(new_speed):
    assert 0 <= new_speed <= 100
    global speed
    current = speed_to_duty(speed)
    target = speed_to_duty(new_speed)
    step = 1 if target > current else -1
    for i in range((current + step), (target + step), step):
        pin.duty(i)
        schedule.run_pending()  # Don't block the scheduler.
        time.sleep_ms(DELAY)
    # If new_speed is 0 then don't leave duty at MIN_DUTY, reduce it all the way to 0.
    if new_speed == 0:
        pin.duty(0)
    speed = new_speed


# ----------------------------------------------------------------------

# Process user entered commands.
def process(line):
    try:
        words = line.split()
        command = words[0][0]
        if command == "s":
            set_speed(int(words[1]))
        elif command == "r":
            reverse()
        elif command == "c":
            set_color(bytes(map(int, words[1:4])))
        elif command == "p":
            machine.deepsleep()
        else:
            # `repr` converts non-printing characters to hex escapes or '\n' etc.
            print("Ignoring: {}".format(repr(line)))
    except Exception as e:
        sys.print_exception(e)


# ----------------------------------------------------------------------

# Set up the web server that serves out ROOT_URL as its main page and
# which handles accepting websocket connections.

poller = select.poll()
slim_server = SlimServer(poller)

ROOT_URL = "https://george-hawkins.github.io/material-lighthouse-controls/"


def request_index(request):
    uuid = hexlify(urandom(16)).decode()
    # GitHub returns stale cached results unless we force things by appending a UUID.
    r = requests.get(ROOT_URL + "?" + uuid)
    request.Response.ReturnOk(r.text)
    r.close()


extractor = Extractor()
ws_manager = WsManager(poller, extractor.consume, process)

# fmt: off
slim_server.add_module(WebRouteModule([
    RegisteredRoute(HttpMethod.GET, "/", request_index),
    RegisteredRoute(HttpMethod.GET, "/socket", ws_manager.upgrade_connection)
]))
# fmt: on

# ----------------------------------------------------------------------

while True:
    for (s, event) in poller.ipoll(0):
        ws_manager.pump_ws_clients(s, event)
        slim_server.pump(s, event)
    slim_server.pump_expire()
    schedule.run_pending()

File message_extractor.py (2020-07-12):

import logging


_logger = logging.getLogger("message_extractor")


# Messages are arbitrary sequences of characters delimited by STX at the start and ETX
# at the end and with a maximum length (specific as a constructor argument here).
# There's no support for escaping STX and ETX within a message and no support for
# characters that require more than one byte.
class Extractor:
    _STX = 2
    _ETX = 3

    def __init__(self, max_message_len=16):
        self.max_message_len = max_message_len

        buffer_len = max_message_len + 1
        buffer = bytearray(buffer_len)

        self._view = memoryview(buffer)
        self._offset = 0

    # `consume` keeps reading data until all currently available data is read.
    # It returns only the last message received, i.e. if you send messages too fast, such
    # that they're arriving quicker than the system's ability to consume them individually
    # then it will discard all but the most recent message.
    def consume(self, readfn):
        finished = False

        while not finished:
            free = len(self._view) - self._offset
            count = readfn(self._view[self._offset : len(self._view)])

            # Break on 0 or None (Stream.readline returns None when no data is available).
            if not count:
                break

            # We're finished when we've clearly hit the end of all currently available data.
            # I.e. we've read less bytes than we had capacity for.
            finished = count < free
            self._offset += count

            # Search backwards in read data for STX. Shift it to 0 position if found.
            start = self._offset - 1
            end = self._offset - count - 1
            if end == -1:
                end = 0
            for i in range(start, end, -1):
                c = self._view[i]
                if c == self._STX:
                    # We discard all but the last message.
                    _logger.warning(
                        "Discarding superseded data {}".format(bytes(self._view[0:i]))
                    )
                    tmp = self._offset - i
                    self._view[0:tmp] = self._view[i : self._offset]
                    self._offset = tmp
                    break

            # The buffer is deliberately one byte longer than the longest valid message.
            # If the buffer is full the message is invalidly long (irrespective of
            # whether the message is otherwise structuraly valid).
            if self._offset == len(self._view):
                _logger.warning(
                    "Discarding oversized data {}".format(bytes(self._view))
                )
                self._offset = 0
            elif self._view[0] != self._STX:
                _logger.warning(
                    "Discarding invalid data {}".format(
                        bytes(self._view[0 : self._offset])
                    )
                )
                self._offset = 0

        if self._offset > 0 and self._view[self._offset - 1] == self._ETX:
            message = str(self._view[1 : (self._offset - 1)], "utf-8")
            self._offset = 0
            # Zero length messages can be used as low-level heartbeats that are always ignored.
            return message if len(message) > 0 else None
        else:
            return None

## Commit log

2020-07-04 Added frizting layouts.
    [breadboard.fzz, perma-proto.fzz]
2020-07-12 Expanded README and fixed issue setting elements of `color`.
    [main.py, message_extractor.py]
2020-08-04 Updated dimensions for bolts for motor body.
